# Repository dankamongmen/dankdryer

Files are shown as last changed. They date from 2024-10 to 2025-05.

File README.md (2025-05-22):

<p align="center">
ESP32, OpenSCAD, and KiCad sources for the Dankdryer, the world's best filament dryer.
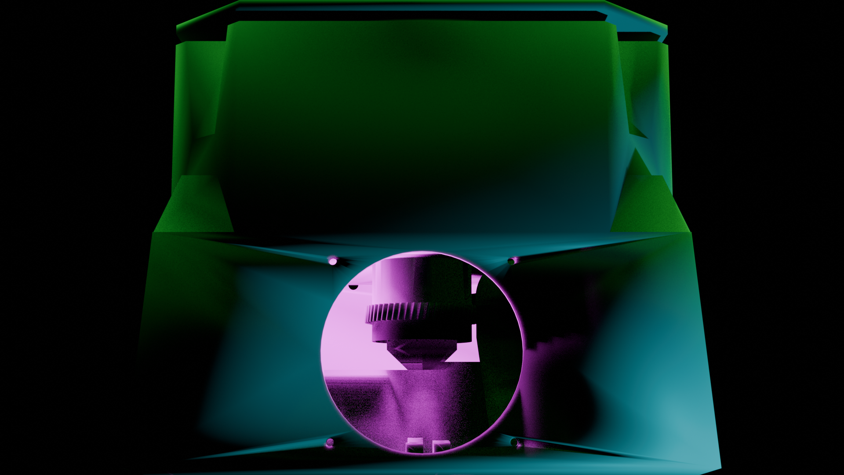
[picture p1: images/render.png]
Side view
 
 a nick black joint
</p>

# Features

* Temperatures up to at least 150℃  when printed with proper materials.
  * Such temperatures are appropriate (necessary) for certain engineering filaments.
  * A high-temperature spool is required at these temperatures.
* Accurate weight sensing throughout to determine how much water has been exorcised.
  * Post contextless deltas to reddit in the heat of dumbass arguments! DATA, bitch!
* Slow rotation like delicious savory meat.
* Equal heating of all the spool's filament.
* Control and reporting over MQTT via WiFi.
* OTA firmware upgrades.
* Isolated hot and cool chambers, with most active equipment in the cool chamber.
* Humidity sensing and temperature sensing in both chambers.
* Entirely open source.

More info at [dankwiki](https://nick-black.com/dankwiki/index.php/Dankdryer).

# Dependencies

The project is built with GNU Make.
Running `make` in the toplevel will attempt to build firmware and STLs.
Building the firmware requires the `esp-idf` library and a configured
ESP-IDF environment (i.e. the various `IDF_*` environment variables
must be set), along with CMake. `idf.py` ought be in your `$PATH`,
and work when invoked.

## Firmware
* [esp-idf](https://github.com/espressif/esp-idf) 5.3+
* [CMake](https://gitlab.kitware.com/cmake/cmake) 3.16+

## 3D models
* OpenSCAD 2024.10+

I use
[BOSL2](https://github.com/BelfrySCAD/BOSL2), which
is included as a submodule.

## PCB
* KiCad 8+

# Construction / BOM

The device as designed requires approximately 600g of high-temperature filament
(PA6-CF, PA6-GF, PAHT-CF, etc.) to print. The exact amount of filament will
depend on material and print settings. Six pieces must
be printed:

 * Hot chamber
 * Cool chamber
 * Top
 * Motor sheath
 * Sheath coupling
 * Spool platform

The hot and cool chamber dominate filament consumption, though the top is
non-negligible.

### Hot chamber

* [230C 110V ceramic heating element](https://www.amazon.com/dp/B0BXNPXXYW)
* [KSD301 175C NC thermal control](https://www.aliexpress.us/item/2251832675942217.html)
* [Hall sensor](https://www.digikey.com/en/products/detail/diodes-incorporated/AH3712Q-P-B/19920700)
* Custom PCB (fabrication cost is negligible; see components below)

We need a temperature sensor and hall effect sensor (and obviously the
heating circuit) in the hot box; nothing else ought be there.

### Cool chamber

* [Greartisan 5RPM 12V DC motor](https://www.amazon.com/dp/B072N867G3/)
* [NEMA plug + rocker switch](https://www.amazon.com/ASHATA-Rocker-Switch-Adapter-Printer/dp/B085VSS1F2)
* [160W 12V AC adapter](https://www.amazon.com/gp/product/B0D7GMVK2F)
* [8dBi antenna](https://www.aliexpress.us/item/3256807262687553.html)
* 5kg bar strain load cell
* 2-to-4 cable splitter
* Custom PCB (fabrication cost is negligible; see components below)

#### PCB components

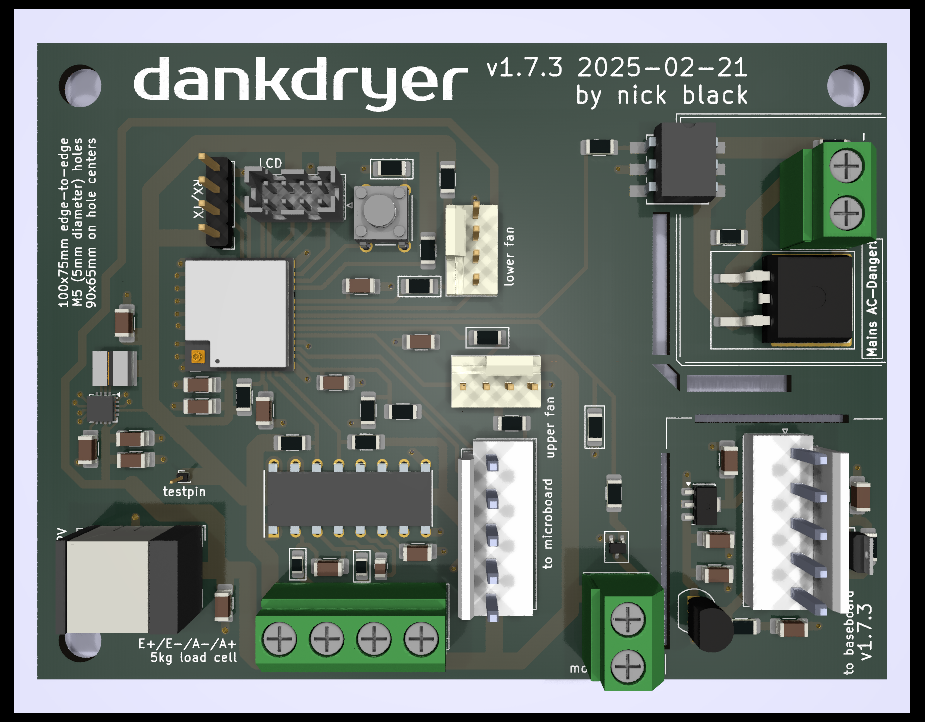
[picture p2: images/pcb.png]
Custom PCB


Generated via Kicad:

|Designator|Footprint|Quantity|Designation|
|---|---|---|---|
|U1|TPS62132|1|TPS62132|
|R4|R_1206_3216Metric_Pad1.30x1.75mm_HandSolder|1|360|
|R2|R_1206_3216Metric_Pad1.30x1.75mm_HandSolder|1|620|
|R6,R8|R_1206_3216Metric_Pad1.30x1.75mm_HandSolder|2|4.7k|
|C15,C16|C_1206_3216Metric_Pad1.33x1.80mm_HandSolder|2|1n|
|SW2|SW_B3F-1000_OMR|1|bootmode|
|R13,R20,R15|R_1206_3216Metric_Pad1.30x1.75mm_HandSolder|3|10k|
|R5,R1,R22|R_1206_3216Metric_Pad1.30x1.75mm_HandSolder|3|680|
|C7,C3,C9,C8,C20|C_1206_3216Metric_Pad1.33x1.80mm_HandSolder|5|0.1u|
|U2|TRANS_AH3712-P-B_DIO|1|AH3712Q-P-B|
|C6,C13|C_1206_3216Metric_Pad1.33x1.80mm_HandSolder|2|22u|
|C10,C17|C_1206_3216Metric_Pad1.33x1.80mm_HandSolder|2|1u|
|IC1|DIP792W51P254L1905H53Q16N|1|NAU7802KGI|
|J10|FanPinHeader_1x04_P2.54mm_Vertical|1|lower fan|
|C19,C2,C1,C14|C_1206_3216Metric_Pad1.33x1.80mm_HandSolder|4|10u|
|J2|JST_VH_B5P-VH-B_1x05_P3.96mm_Vertical|1|to microboard|
|J4|TerminalBlock_bornier-2_P5.08mm|1|heater|
|J8|TerminalBlock_bornier-2_P5.08mm|1|motor|
|J7|FanPinHeader_1x04_P2.54mm_Vertical|1|upper fan|
|R9,R19|R_1206_3216Metric_Pad1.30x1.75mm|2|15k|
|U6|XCVR_ESP32-C6-MINI-1U-H4|1|ESP32-C6-MINI-1U|
|J11|PinHeader_1x01_P1.00mm_Vertical|1|testpin|
|R16|R_1206_3216Metric_Pad1.30x1.75mm_HandSolder|1|412|
|J13|BarrelJack_Wuerth_6941xx301002|1|barreljack|
|R7|R_1206_3216Metric_Pad1.30x1.75mm_HandSolder|1|1.62k|
|C4,C18|C_1206_3216Metric_Pad1.33x1.80mm_HandSolder|2|.01u|
|J5|TerminalBlock_bornier-4_P5.08mm|1|5kg load cell|
|R10,R11|R_0805_2012Metric_Pad1.15x1.40mm_HandSolder|2|47|
|U5|TO-92_Inline|1|LM35-LP|
|R3|R_1206_3216Metric_Pad1.30x1.75mm_HandSolder|1|100|
|L1|IND_IFSC_1515AH_VIS|1|2.2u|
|R14|R_1206_3216Metric_Pad1.30x1.75mm_HandSolder|1|3.3k|
|OC1|MOC306XS_LTO|1|MOC3063S|
|C12|C_1206_3216Metric_Pad1.33x1.80mm_HandSolder|1|3.3n|
|C11|C_0805_2012Metric_Pad1.18x1.45mm_HandSolder|1|470p|
|R21|R_1206_3216Metric_Pad1.30x1.75mm_HandSolder|1|68|
|J9|PinHeader_1x04_P2.54mm_Vertical|1|UART|
|J6|JST_PHD_B8B-PHDSS_2x04_P2.00mm_Vertical|1|LCD|
|J3|JST_VH_B5P-VH-B_1x05_P3.96mm_Vertical|1|to baseboard|
|Q3|TO-263-2|1|T1210-800G|
|Q2|SOT-323_SC-70|1|SSM3K127TU|
|R12|R_1206_3216Metric_Pad1.30x1.75mm_HandSolder|1|330|
|U3|SOT-89-3|1|HT7550|

# MQTT

MQTT is used to report status and to accept commands.

## Controls

* `NAME/control/tare`: tare using the last weight read
* `NAME/control/dry`: takes as argument a string "DRYS/TEMP", where DRYS and TEMP are unsigned integers
    specifying the number of seconds to dry, and the temperature to dry at. Any ongoing drying operation
    will be replaced with the newly specified one. Specifying zero for DRYS will cancel any ongoing
    drying operation.
* `NAME/control/lpwm`: takes as argument a hexadecimal number between 0 and 255, left-padded with zeroes
    so as to be exactly two digits, i.e. "00".."ff". Sets the lower fan's PWM.
* `NAME/control/upwm`: takes as argument a hexadecimal number between 0 and 255, left-padded with zeroes
    so as to be exactly two digits, i.e. "00".."ff". Sets the upper fan's PWM.
* `NAME/control/factoryreset`: takes no arguments. Blanks the persistent storage, disables the motor
    and heater, and reboots.

# Renderings

View from the top of the lower chamber by itself, with the AC
adapter and motor assembly present.

<p align="center">
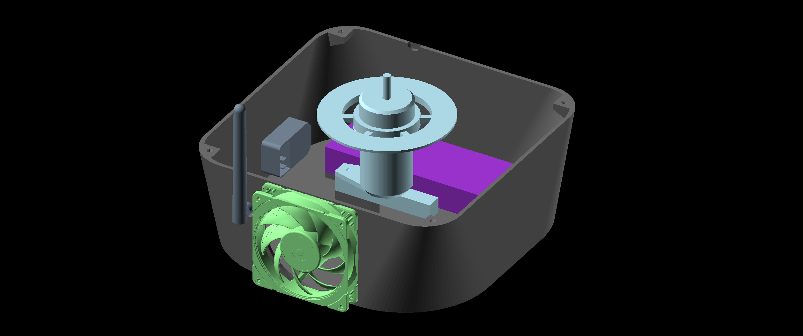
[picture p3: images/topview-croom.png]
Top view, lower chamber

</p>

Combined OpenSCAD render for mating testing.

<p align="center">
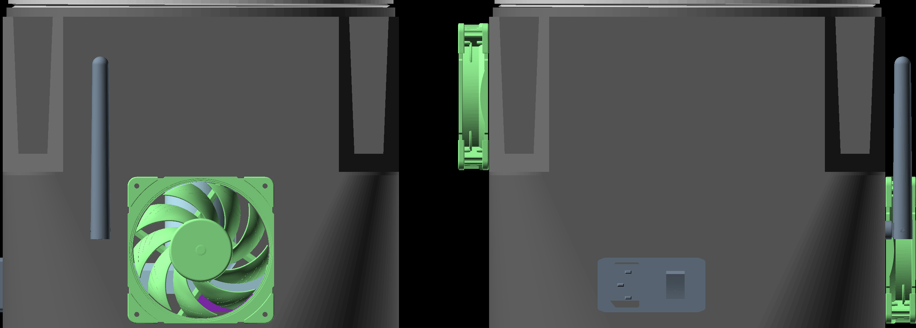
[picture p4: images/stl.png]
Combined render
 
</p>

# Questions

* How does air flow? Let's get some visible air and test it.
* What all could we accomplish by reading RFID?

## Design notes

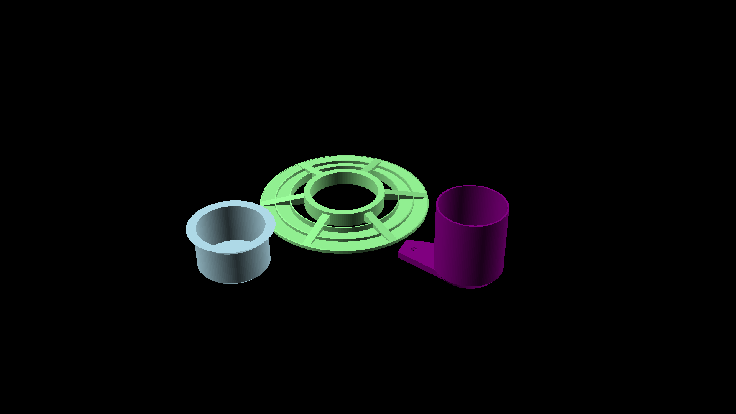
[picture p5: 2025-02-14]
webpage/coupling.png

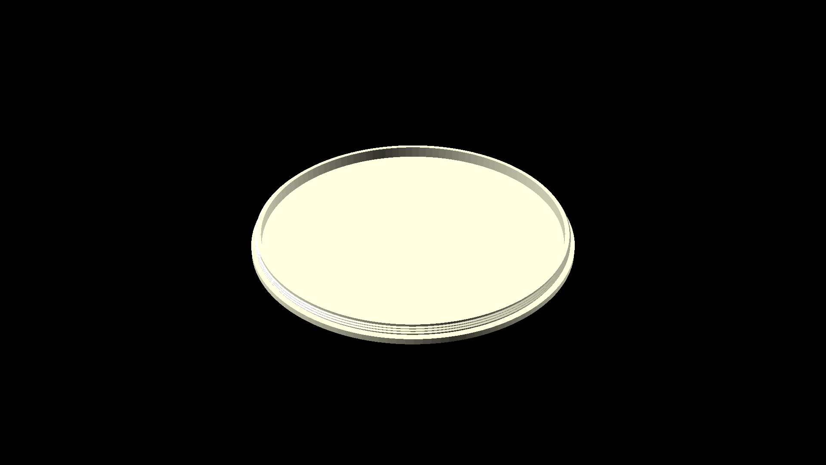
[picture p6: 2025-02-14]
webpage/top.png

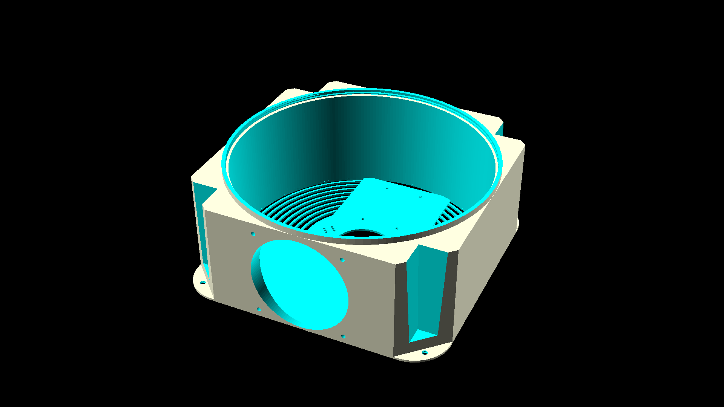
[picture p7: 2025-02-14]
webpage/hotbox.png

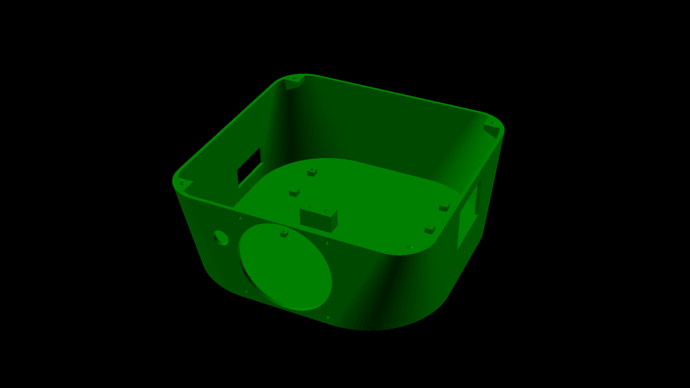
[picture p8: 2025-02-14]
webpage/croom.png

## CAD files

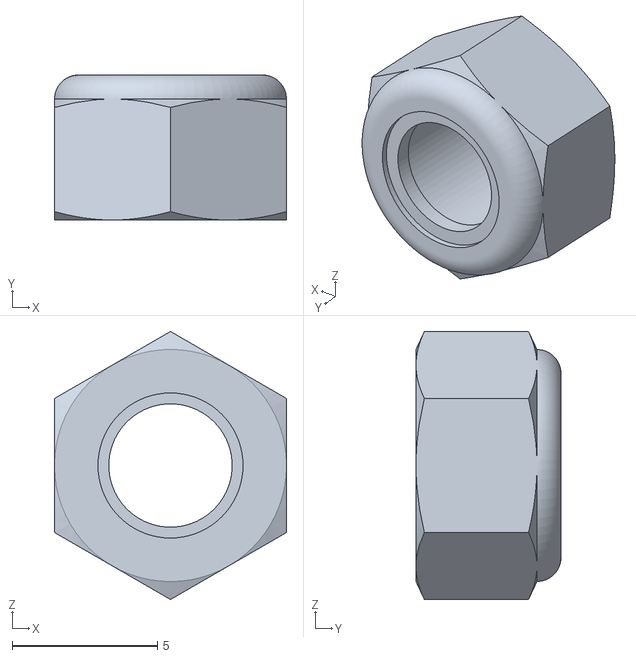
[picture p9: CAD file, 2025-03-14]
scad/m5nyloc.stl
8.00 x 5.00 x 9.24

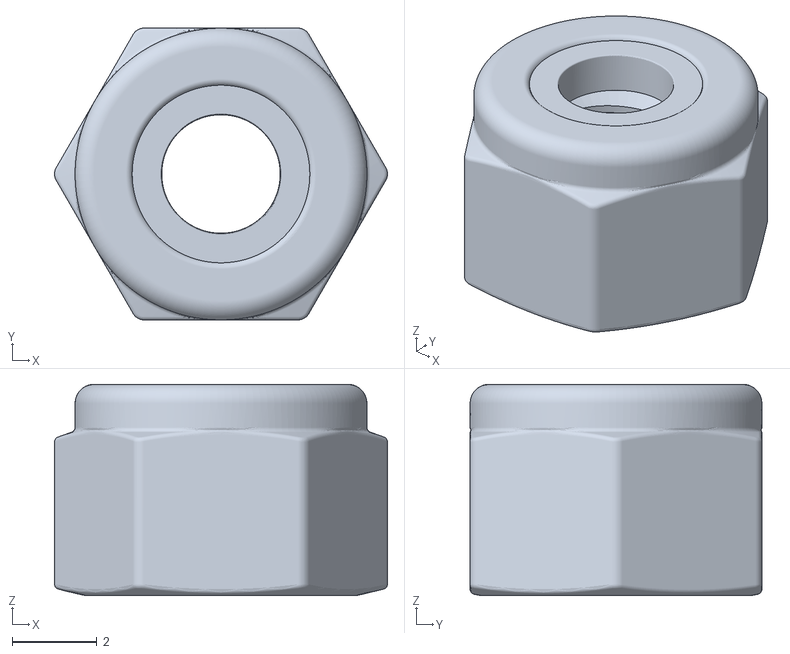
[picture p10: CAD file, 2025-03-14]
scad/m4nyloc.stl
7.87 x 6.90 x 5.00

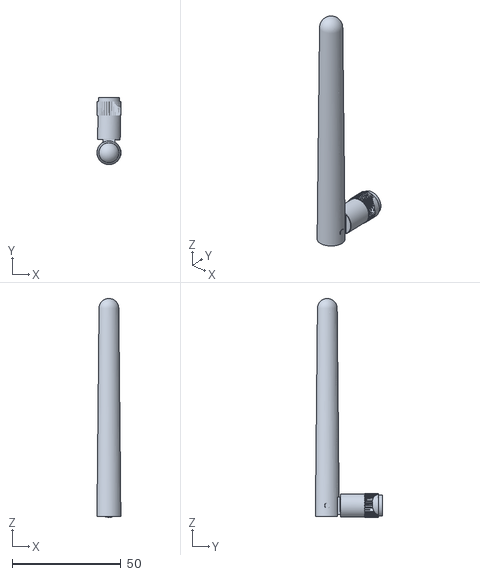
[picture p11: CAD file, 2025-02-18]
scad/antenna_WiFi_RP-SMA_conn.stl
11.1 x 30.9 x 100.5

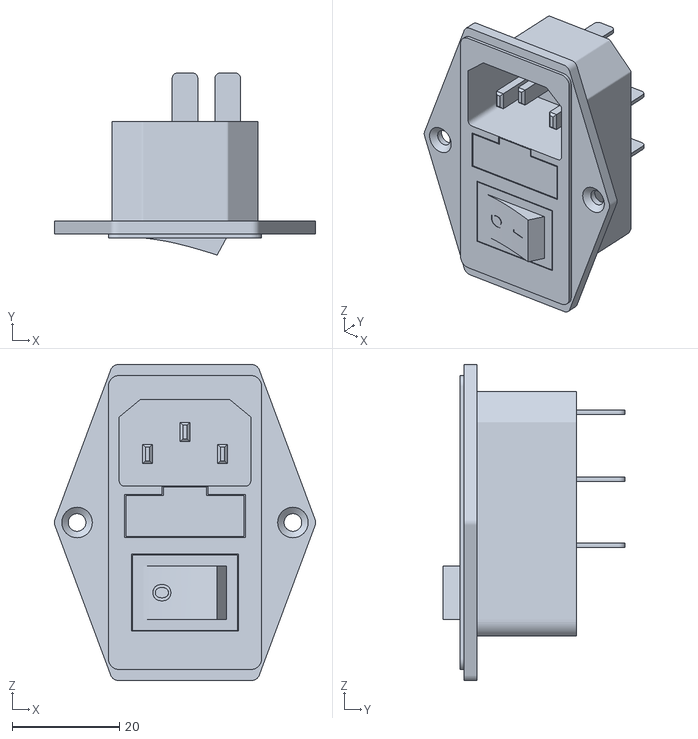
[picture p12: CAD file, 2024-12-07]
scad/iec.stl
48.8 x 34.0 x 59.0

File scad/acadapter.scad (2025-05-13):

include <core.scad>
include <BOSL2/std.scad>

// hole for four-prong rocker switch + receptacle.
// https://www.amazon.com/dp/B0CW2XJ339
// 45.7mm wide, 20mm high. if we can't print
// the bridge, we'll have to reorient it.
// model with fuse is 30mm
//rockerh = 20;
rockerh = 30;
rockerw = 46.3; // a bit of skoosh viz 45.7
module rockerhole(iech){
	translate([-botinalt - 2, 0, iech / 2 + 25]){
		rotate([90, 0, 0]){
			rotate([0, 180 - theta, 0]){
				difference(){
					cube([croomwall + 2, rockerw, rockerh], true);
					// two thin clips to hold the plug in
					// depth: 1mm height: 1.5mm
					translate([-1, 0, 0]){
						union(){
							translate([0, 0, rockerh / 2 - 0.75]){
								cube([1, rockerw, 1.5], true);
							}
							translate([0, 0, -rockerh / 2 + 0.75]){
								cube([1, rockerw, 1.5], true);
							}
						}
					}
				}
			}
		}
	}
}

//acadapterh = 30; // old model
acadapterh = 22;
acadapterw = 50;
acadapterl = 135;
acmounth = 6;

// the stand without the plug, since our AC
// adapters only have two places to screw
module acadapterstand(){
	translate([acadapterl / 2 - 0.5, -acadapterw / 2 + 7, acmounth / 2]){
		diff(){
			cuboid([8, 6, acmounth], 
					rounding=-1, edges=BOT)
				edge_profile(except=[TOP,BOT])
					mask2d_roundover(r=1);
		}
	}
}

// 60mm wide total
// screw holes are 6mm in from sides, so they start at
// 6mm (through 10mm) and 50mm (through 54mm)
// they have 2mm radius and 3mm height
module acadapterstands(){
	translate([0, acadapterw, 0]){
     	acadapterstand();
        mirror([0, 1, 0]){
			acadapterstand();
			mirror([1, 0, 0]){
				acadapterstand();
            }
        }
		mirror([1, 0, 0]){
			acadapterstand();
		}
    }
}

// hole in the AC adapter stand for screw
module acadapterhole(){
	translate([acadapterl / 2 - 0.5, -acadapterw / 2 + 7, 0]){
		holed = 3.6;
		ScrewThread(holed, acmounth);
	}
}

// screw holes for mounting ac adapter in two corners
module acadapterholes(){
	translate([0, acadapterw, 0]){
		acadapterhole();
		mirror([0, 1, 0]){
			mirror([1, 0, 0]){
				acadapterhole();
			}
		}
	}
}

module acadapter(){
	translate([0, 0, acadapterh / 2]){
		cube([acadapterl, acadapterw, acadapterh], true);
	}
}

/*difference(){
	acadapterstands();
	acadapterholes();
}*/
//acadapter();

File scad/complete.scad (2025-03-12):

include <core.scad>
use <hotbox.scad>
use <croom.scad>
use <coupling.scad>
use <top.scad>

multicolor("lightgreen"){
	translate([0, -109, -41]){
		rotate([theta, 0, 0]){
			rotate([0, 90, 90]){
				scale(17){
					import("noctua_nf-a12_fan.stl");
				}
			}
		}
	}
}

multicolor("black"){
	drop(){
		translate([0, 50, wallz]){
			acadapter();
		}
	}
	translate([-110, -30, -60]){
		rotate([0, 180 - theta, 0]){
			intersection(){
				rotate([270, 0, 0]){
					rotate([0, 0, 270]){
						import("iec.stl");
					}
				}
				cube([40, 120, 30], true);
			}
		}
	}
	translate([-55, -118, -35]){
		import("antenna_WiFi_RP-SMA_conn.stl");
	}
}

multicolor("dimgrey"){
    drop(){
        croom(20);
    }
}

multicolor("green"){
	drop(){
		pcb();
	}
}

multicolor("lightblue"){
    drop(){
        assembly();
    }
}

// top portion
if(!OPENTOP){
	rotate([0, 0, $t]){
		drop(){
			spool();
		}
	}

	multicolor("lightgreen"){
		translate([0, 109, 43]){
			rotate([0, 90, 90]){
				scale(17){
					import("noctua_nf-a12_fan.stl");
				}
			}
		}
	}

	multicolor("silver"){
			translate([0, 0, totalz + 2]){
					mirror([0, 0, 1]){
							top();
					}
			}
	}

	multicolor("dimgrey"){
			rotate([0, 0, 180]){
					hotbox();
			}
	}
}

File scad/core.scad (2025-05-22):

include <BOSL2/std.scad>
include <BOSL2/screws.scad>
use <threads.scad>

$fn = 128;

current_color = "ALL";

module multicolor(color, opacity=1) {
	//if (current_color != "ALL" && current_color != color) {
		color(color, opacity){
			children();
		}
	/*} else {
		// ignore
	}*/
}

module idtext(){
  text3d("v2.8.4", h=1.2, size=6);
}

// we need to hold a spool up to 205mm in diameter and 75mm wide
spoold = 205;
spoolh = 75;
// 80mm fan; use sin(theta)80 if we're sloped.
// 81 is a multiple of both 0.3 and 0.2.
hotz = 81;
spoolholed = 55;
tpitch = 1.8; // multiple of 0.3 and 0.2
// we'll want some room around the spool,
// but the larger our chamber, the more heat lost.
wallz = 1.8; // bottom thickness; don't want much
gapxy = 1; // gap between spool and walls; spool/walls might expand!
wallxy = 5;
// height of threaded, mated section at the top
// (and probably soon at the middle FIXME).
// ensure it's a multiple of both 0.2 and 0.3 to
// support both .4mm and .6mm nozzle layer heights.
ttopz = 0.2 * 0.3 * 100; // 6mm
// spool distance from floor and ceiling.
elevation = (hotz - spoolh) / 2;
chordxy = 33;
innerr = spoold / 2 + gapxy;
totalxy = spoold + wallxy * 2 + gapxy * 2;

ctopz = wallz;
croomz = wallz + ctopz + hotz;
totalz = hotz + wallz + ttopz + elevation;
locknuth = 5; // locknuts go atop mounting rods

// thickness of croom xy walls (bottom is wallz)
croomwall = 3;
// the outer radii on our top and bottom
botrad = totalxy * sqrt(2) / 2;
toprad = totalxy * sqrt(2) / 2;
// the inner radii on its top and bottom
botinrad = botrad - croomwall * sqrt(2);
topinrad = toprad - croomwall * sqrt(2);
// distances from center to mid-outer wall
topalt = toprad / sqrt(2);
botalt = botrad / sqrt(2);
topinalt = topinrad / sqrt(2);
botinalt = botinrad / sqrt(2);
botround = 90;
topround = 70;
adj = (botrad - toprad) / sqrt(2);
theta = (90 - atan(-croomz / adj));

flr = -croomz + wallz; // floor z offset
mh = wallz; // mount height
shieldw = 88;

module topbottom(height){
    linear_extrude(wallz){
        polygon(opoints);
    }
}

// cXcX3mm cube bottom plus (rh + th) d-wide riser
// rh is smooth length, th is threaded length
module mount(c, rh, th, d){
	ct = 3;
	translate([0, 0, ct / 2]){
		cube([c, c, ct], true);
		translate([0, 0, ct / 2]){
			RodStart(d, rh, th,
			         thread_diam=d - 0.5,
					 thread_pitch=0);
		}
	}
}

module foursquare(){
    children();
    mirror([1, 0, 0]){
        children();
		mirror([0, 1, 0]){
			children();
		}
    }
    mirror([0, 1, 0]){
        children();
    }
}

module rot(deg){
    rotate([theta + deg, 0, 0]){
        children();
    }
}

// spacing between the 4.3mm diameter holes is
// 71.5mm, so 8.5 / 2 == 4.25 from hole center
// to side. triangle with bases 2 * 8.5 == 17
module fanmountur(h){
    rotate([90, 0, 0]){
        // really want 4.3 but 4.5 is a multiple of
		// 0.3, and these will be horizontal
		// FIXME
		//ScrewThread(4.5, h, pitch=3);
		cylinder(h, 4.5 / 2, 4.5 / 2, true);
    }
}

module fanmountsider(h, d){
    translate([0, 0, d]){
        fanmountur(h);
    }
    mirror([0, 0, 1]){
        translate([0, 0, d]){
            fanmountur(h);
        }
    }
}

module fanmounts(h){
    r = 4.3;
    dist = 71.5;
    translate([dist / 2, 0, 0]){
        fanmountsider(h, dist / 2);
    }
    mirror([1, 0, 0]){
        translate([dist / 2, 0, 0]){
            fanmountsider(h, dist / 2);
        }
    }
}

//fanmounts(9);

module fanhole(h){
	fanmm = 80 - 5;
    rotate([90, 0, 0]){
        cylinder(h, fanmm / 2, fanmm / 2, true);
    }
    fanmounts(h);
}

//fanhole(9);

loadcellh = 12.7;
//loadcelll = 76;
loadcelll = 80;
// there is 5mm from each side to the center of
// hole closest to it, and 15mm between the centers
// of holes on a side. there are 40mm between the
// centers of the two inner holes. 80mm total.
loadcellmountholegap = 15;
loadcellmountholeside = 5;
loadcellmountholecgap = 40;
loadcellmountl = loadcellmountholeside +
                 loadcellmountholegap +
				 loadcellmountholecgap / 4;
loadcellmounth = 17;
loadcellsupph = 4;
loadcellmountw = loadcellh;
// we need the load-side holes of the load cell
// to be centered around the chamber center.
// the load-side center is at (loadcellmountholegap
// plus loadcellmountholeside) / 2.
loadcelloffx =
 (loadcellmountholegap + loadcellmountholeside) / 2
 - (loadcelll / 2);
module loadcell(){
    // https://amazon.com/gp/product/B07BGXXHSW
    cube([loadcelll, loadcellh, loadcellh], true);
}

// load cell mounting base with two threads
module loadcellmount(baseh){
    difference(){
		translate([0, 0, baseh / 2]){
			diff(){
				cuboid([loadcellmountl + 2,
						loadcellh + 2, baseh], 
						rounding=-5, edges=BOT)
					edge_profile(TOP)
						mask2d_roundover(r=2);
			}
        }	
        translate([-loadcellmountholegap / 2, 0, 0]){
			ScrewThread(5, baseh);
        }
        translate([loadcellmountholegap / 2, 0, 0]){
			ScrewThread(5, baseh);
        }
    }
}

//loadcellmount(loadcellmounth);

// height of inverse cone supporting bearing holder
couplingh = 10;
bearingh = 9; // height ("width") of bearing
bearingr = 30 / 2; // bearing outer radius
bearinginnerr = 10 / 2; // bearing inner radius
bearingwall = 2;
shaftr = bearinginnerr - 1;

module drop(){
    translate([0, 0, -croomz]){
        children();
    }
}

// motor is 37x75mm diameter gearbox and 6x14mm shaft
motorboxh = 70;
motorboxd = 37;
motorshafth = 40; // sans worm: 14
motortheta = -60;
motormounth = 61;
module motor(){
    cylinder(motorboxh, motorboxd / 2, motorboxd / 2, true);
    translate([0, 0, motorboxd]){
        cylinder(motorshafth, 6 / 2, 6 / 2, true);
    }
}

motorholderh = 3;
mlength = motorboxh + motorholderh;

module lowercoupling(){
	// the center must be in the dead center
	// of the structure.
	outerr = (motorboxd + 2) / 2;
	// we add 0.5mm for the polycarbonate (1 for
	// CF/GF), as it has no flex (0.25 to innerr)
	innerr = motorboxd / 2 + 0.25;
	// hole in middle to accommodate 10mm shaft
	holer = 10 / 2;
	boltheadh = 4;
	boltheadr = 3.5;
	th = loadcellsupph + boltheadh;
	couplingh = 40;
	// primary motor holder
	difference(){
		translate([0, 0, couplingh / 2 + loadcellsupph]){
			cylinder(couplingh, outerr, outerr, true);
		}
		translate([0, 0, loadcellsupph + couplingh / 2]){
			cylinder(couplingh, innerr, innerr, true);
		}
	}
	// fill in the bottom
	difference(){
		union(){
			cylinder(loadcellsupph,
					(motorboxd - loadcellsupph) / 2,
					outerr);
			translate([0, 0, loadcellsupph]){
				cylinder(boltheadh, outerr, outerr);
			}
		}
		cylinder(th, holer, holer);
		translate([0, 0, loadcellsupph + boltheadh / 2]){	
			// two M4 screws couple to the
			// load cell, but only the heads
			// remain
			// printing polycarbonate, which
			// tends to shrink). we then need
			// embed the 7x4 head in the floor
			translate([-loadcellmountholegap / 2, 0, loadcellsupph / 2]){
				rotate([180, 0, 0]){
					RodStart(boltheadr * 2,
							 boltheadh,
							 thread_len=loadcellsupph,
							 thread_diam=5);
				}
			}
			translate([loadcellmountholegap / 2, 0, loadcellsupph / 2]){
				rotate([180, 0, 0]){
					RodStart(boltheadr * 2,
							 boltheadh,
							 thread_len=loadcellsupph,
							 thread_diam=5);
				}
			}
		}
		// holes in the bottom for wires, polarity
		// legend, and also boltholes
		translate([0, 0, th / 2]){
			translate([0, innerr - 7, 0]){
				cylinder(th, 3, 3, true);
			}
			translate([0, -innerr + 7, 0]){
				cylinder(th, 3, 3, true);
			}
		}
		// designate positive side
		translate([4, -15, 0]){
			linear_extrude(th){
				text("+", size=7, font="Prosto One");
			}
		}
	}
}

/*bracel = loadcelll / 2 - loadcellmountl;
translate([-bracel + 3, 0, 0]){
	loadcellmount(loadcellsupph + 1);
}*/
//lowercoupling();
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

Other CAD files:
scad/coupling.scad
scad/croom.scad
scad/hotbox.scad
scad/lcd.scad
scad/lowercoupling.scad
scad/threads.scad
scad/top.scad

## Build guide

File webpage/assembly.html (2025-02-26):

# Assembly

## Not necessary for preassembled units!

Six objects are printed using four generated STL files. They ought be printed in the generated orientations.

- Top
- Upper (hot) chamber
- Lower (cool) chamber
- Internal components (load cell coupling, motor coupling, spool platform)

The OpenSCAD files can be found on Github (https://github.com/dankamongmen/dankdryer/tree/master/scad). The zipped STLs can be found here, and a 3MF is also available (https://nick-black.com/dankdryer.3mf). I print them with the Arachne perimeter generator and infill combination using cross hatch for the sparse infill. Using Polymaker Fiberon PA6-CF20 (nylon-6 + carbon fiber) with these settings, all components come in just over 600g.

Warp-free printing is essential. Warping of the internal components or the lower chamber can result in the spool not sitting level. Warping of the upper chamber can result in it failing to mate to the lower chamber.

1. Push the 175℃ thermostat through the bottom of the upper chamber.
2. Push the LM35 through-hole thermostat through the three small holes in the floor of the upper chamber.
3. Use four M4 screws to mount the ceramic heating element to the floor of the upper chamber.
4. Use four M5 screws to mount one of the 80mm fans to the outside of the upper chamber. The logo ought be facing out; this fan is an exhaust.
5. Insert the power plug/rocker switch unit into the rectangular hole on the side of the lower chamber. It ought not move once inserted. Secure it with hot glue.
6. Use two M5 screws to mount the AC adapter to the floor of the lower chamber, on the side opposite the intake fan.
7. Wire the plug/switch to the AC adapter.
8. Place the AC shield atop the AC wiring, and push it down. Secure it with hot glue.
9. Use four M5 screws to mount the PCB to the floor of the lower chamber, next to the intake fan.
10. Insert the antenna into the antenna hole to the left of the lower chamber's fan. Secure it with hot glue.
11. Connect the antenna to the U.FL connector on the PCB.
12. Use four M5 screws to mount the other 80mm fan to the outside of the lower chamber. The logo ought be facing in; this fan is an intake.
13. Connect the lower fan to the fan connector marked "lower" on the PCB.
14. Connect the upper fan to the fan connector marked "upper" on the PCB.
15. Use two M5 screws to mount the load cell to the central riser in the lower chamber.
16. Insert the motor into the motor coupling, ensuring the positive terminal mates to the hole marked '+'. The terminals ought go through the holes.
17. Wire the motor to the PCB.
18. Wire the heating element to the 175℃ thermostat.
19. Wire the heating element to the PCB.
20. Wire the 175℃ thermostat to the PCB.
21. Place the upper chamber atop the bottom chamber, matching the four holes.
22. Use four M5x35 bolts to securely mate the two chambers.
23. Push the spool platform down around the motor coupling.
24. Push the motor coupling down around the rotor and the top of the motor. The platform ought provide a level surface.
25. Place the top into the upper chamber.

### Contents of the kit

These are subject to change.

1. The Dankdryer PCB.
2. 120VAC → 12VDC adapter.
3. 2x 80mm 12VDC be quiet! Pure Wings 2 (https://www.bequiet.com/en/casefans/506) 4-pin fans.
4. 5kg load cell.
5. 12VDC brushed 5RPM motor.
6. NEMA plug + rocker switch.
7. RP-SMA antenna + U.FL adapter.
8. Wago 1x2→2x2 splitter.
9. 230℃ ceramic heating element.
10. 175℃ thermostat.
11. Roof microboard (currently perfboard + throughhole components).
12. Small bar magnet.
13. Bolts and appropriately preterminated wires.

copyright © nick black 2024–2025

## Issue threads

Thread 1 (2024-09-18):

open up AC hole

dankamongmen, 2024-09-18:
the side hole for our ac cabling is too small. i think it's currently 5mm. 7mm is probably better. we might also want to see about moving it to the fan side, or putting a TPU gasket in there -- right now it's on a hotpath for air, and we'll likely lose some out of it.

dankamongmen, 2024-09-18:
A naive enlargement shows an obstruction on the top. What could this be?
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

dankamongmen, 2024-09-18:
yeah it starts around -72.3 whatever size we make the hole

dankamongmen, 2024-09-18:
are we maybe improperly tilted?

dankamongmen, 2024-09-18:
lengthening the cylinder eliminates this. that makes sense if we're shorter than the wall thickness, but then wouldn't we have seen it at 5?

we don't have an explicit calculation for wall thickness on the croom. i guess it would be `(0.05 * totalxy) / 2`? let's see what that is...5.325. and we were 10, so yeah, i don't think that makes sense. oh, our cylinder could be misplaced, though, yeah that's surely it. let's fix it the right way, then.

dankamongmen, 2024-09-18:
you know what? i think we're improperly titled, as well...

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

dankamongmen, 2024-09-18:
holy shit, i've been misunderstanding the effects of `scale()` this entire time. we're calculating different wall thicknesses at the bottom and top because *the walls have different thickness at bottom and top*, with the wall being thinner at the top. think of it: scaling to 95% everywhere doesn't hold the wall thickness constant, dumbass. but we've been thinking it would for whatever reason.

alright, rather than using `scale()`, use `hull()` and two `polygon()`s. update everything that works off 0.95 multipliers. use the same radii to the outer walls that we have now:

```c
toprad = outerxy / 2;
botrad = totalxy * sqrt(2) / 2;
```

with a `$fn=4` instance of `cylinder()`, then a polygon at `0.95 * botrad`, then a polygon at `toprad - 0.05 * botrad`, with a `hull()` over it. actually, no---`botrad` is distinct from `botrad - croomz`, which is where we want the recess to start. ok, the right triangle drops an altitude from the `toprad`. that hits an outer corner via `sqrt(2) * (0.05 * botrad)`. oh wait we can do this more easily: `-flr / croomz * sqrt(2) * (0.05 * botrad)`

ok i'm just goin to redefine this more sensibly:
```
totalxy = spoold + wallxy * 2 + gapxy * 2; // hotbox altitude * 2. unchanged.
outerxy = (totalxy + 14) * sqrt(2); // hotbox radius. unchanged to reduce invalidations, though arbitrary
toprad = outerxy / 2; // unchanged
botrad =
```

dankamongmen, 2024-09-18:
ok, i've enlarged it to 7mm diameter, and placed it so that there is no obstruction. but it's longer than it ought be. reduce it when we fix #13.

Closed 2024-09-18.

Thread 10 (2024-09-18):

Design an air shield for the load cell

dankamongmen, 2024-09-18:
We cannot allow the fan to blow air over the load cell, as it would disturb our readings. Instead, there ought be an air shield surrounding (but *not* touching) the central shaft. The gear needs to be accessible by the motor, so we'll either need some gap in the air shield, or for it only to go up to the gear. I'm not sure which is better. If it does go all the way up, it ought mate to the central hole in the hotbox. In that case, we'd probably just want corner mounts for the shield where it intersects the gear. In no case ought fasteners be required (except to mount the shield to the croom's bottom).

dankamongmen, 2024-09-20:
Rather than being a distinct part, let's fold this into the lower mount and the croom. The bottom can be a part of the croom, so long as it fits inside the top part of the shield. This will eliminate a part and four screws, strengthen the shield, and make the lower coupling easier to print.

dankamongmen, 2024-09-20:
Though this might make it difficult to attach the load cell to the croom...

dankamongmen, 2024-09-20:
i think we can actually just put the entire thing on the croom, so long as we leave room on the lower coupling to stick an allen wrench down there and secure the load cell to its mount. i've gone ahead and made that change to the LC, which i think is an improvement in any case simply due to less material/weight.

dankamongmen, 2024-10-15:
it's there now, as part of croom.

Closed 2024-10-15.

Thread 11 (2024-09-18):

Design the central shaft

dankamongmen, 2024-09-18:
We need a central shaft on which the magic can happen. It ought fit within the air shield (see #10). It must be mounted to the load cell. It should be as light as possible. It must not receive support from anything but the load cell, or our weight sensing will get wrong results. I'm imagining an upside-down L mounted to the load cell's side and coming out to the center. It then expands into a walled recess into which a bearing is placed. From that bearing arises the central driveshaft. There will be a spacer, then the central gear (and see #10 regarding its effects on shield design). At the top, it expands into a platter onto which the spool will be placed.

Considerations:
* the platter is significantly wider than the shaft. How do we make this stable?
* Right now, the load cell is mounted to the floor of the croom. Any height by which we elevate it reduces the height of the shaft, adding stability. How tall can we take it? The motor would need be elevated a corresponding amount.
* How to keep the spool from moving?

dankamongmen, 2024-09-22:
i think we ought print the platter distinct from the shaft itself, so let's go ahead and whip that up. it ought be a wide circle (maybe half the spool diameter) and a small circle (just about the central hole size) with a `hull()` taken over them. there ought be a hollow column, almost the small circle's size. then another hollow cylinder ought plug in, which can go into the middle of the spool. this way we can have multiple columns, one for each spool size, which will keep them from shifting.

dankamongmen, 2024-10-05:
alright, this is working!

Closed 2024-10-05.

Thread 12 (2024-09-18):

thicken hotbox walls and make croom walls thinner

dankamongmen, 2024-09-18:
Croom walls too thick, hot walls too thin. Let's do 5 up top (we should keep the floor at 3, I think) and 3 on the bottom. Right now I think we have the inverse. Better to do this sooner rather than later, as it likely has effects on numerous things.

dankamongmen, 2024-09-18:
so first we need change `wallxy` from 2 to 5. `wallz`, the hotbox bottom, is by the way 2 not 3; let's change that to 3. this will increase `totalxy` by 6 and `totalz` by 1. a lot of things key off of `totalxy`, which we can't really reduce (it's the sum of `spoold + wallxy * 2 + gapxy * 2`), so we'll need deal with that. on the plus side, maybe this will make #4 easier.

dankamongmen, 2024-09-18:
mounting holes remain perfectly lined up; i think we're good up top...we haven't thinned out the bottom yet, though.

dankamongmen, 2024-09-18:
i don't think we can thin out the bottom until we've addressed the changing thickness of those walls (see #1, which i'm going to move into its own bug -- done, #13). i reduced `gapxy` from 2 to 1 to get 2mm back.

dankamongmen, 2024-09-18:
the croom xy walls are now a mere 2mm.

Closed 2024-09-18.

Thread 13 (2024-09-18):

croom walls get thinner as they rise

dankamongmen, 2024-09-18:
See #1 for initial exploration. The thickness of the croom walls change along the z axis when we reduce it with `scale()`. Instead, define the core via explicit polygons and `hull()` operations. Per #12, the croom walls ought only be 3mm thick. They're currently 5.825mm at their widest point, and 5.475 at their thinnest. This thinning ought significantly reduce material and print time; making them the same thickness throughout ought significantly reduce complexity.

dankamongmen, 2024-09-18:
Once we've done this, we'll need recalculate angles for the fan mount and the AC adapter hole. This is thus a prerequisite for both #1 and #12.

dankamongmen, 2024-09-18:
the xy walls now enjoy constant thicc.

Closed 2024-09-18.

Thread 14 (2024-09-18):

report all status over mqtt

dankamongmen, 2024-09-18:
over mqtt, we need to report:

 * both chamber temps
 * fan pwms
 * fan rpms
 * motor status
 * heater status
 * time left on drying run
 * target temp
 * uptime
 * version

dankamongmen, 2024-10-07:
we're reporting everything we measure. as we measure more, we'll add them.

Closed 2024-10-07.

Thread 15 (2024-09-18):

allow configuration over mqtt

dankamongmen, 2024-09-18:
we need to allow the device to be configured over mqtt. at minimum, this would involve:

* set the absolute drying time remaining
* set the target temperature for any drying

the target temperature ought have a default of 80. the absolute dry time remaining ought have a default of 0.

dankamongmen, 2024-10-07:
we're now supporting `mpwm`, `lpwm`, and `upwm`. these are all low-level controls which i don't really intend to expose to the user, who ought be using `dry`, but this will allow us to test.

dankamongmen, 2024-10-07:
confirmed `lrpm` and `urpm` work properly!

Closed 2024-10-07.

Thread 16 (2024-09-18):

get on wifi and talk to mqtt broker

dankamongmen, 2024-09-18:
we don't currently get on the wifi. do so. it ought be done in the main loop, not `setup()`, because we'll need to reconnect. once that's done, add mqtt connection (and reconnection). necessary for #15 and #14. give feedback via the LED.

dankamongmen, 2024-09-19:
https://docs.espressif.com/projects/esp-idf/en/stable/esp32s3/api-guides/wifi.html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

dankamongmen, 2024-09-19:
let's do it without some intermediary library. Espressif ships their own MQTT client now, so we oughtn't need worry about deps in that stack.

dankamongmen, 2024-09-25:
i'm pretty certain our continuing issues are due to using the arduino-style project and build. let me try building one of their examples using `arduino-cli` and see what happens...

dankamongmen, 2024-09-25:
nope, i was able to build the esp-idf STA example and it connected to my wifi just fine, and pulled down an IP. hrmm...

dankamongmen, 2024-09-25:
ahhh, looks like we needed `esp_netif_create_default_wifi_sta()`. with that call, we properly pull a DHCP lease. alright, excellent.

dankamongmen, 2024-09-25:
yep, with that we are connecting to MQTT and broadcasting mDNS!

```
E..:....@.H...X...X....5.&.k.............mqtt.orthanc.....
19:05:52.609735 IP 192.168.88.1.53 > 192.168.88.165.59396: 48591* 1/0/0 A 192.168.88.1 (46)
E..J..@.@.U	..X...X..5...67..............mqtt.orthanc...................X.
19:05:52.685910 IP 192.168.88.165.60678 > 192.168.88.1.1883: Flags [S], seq 2910239765, win 5760, options [mss 1436], length 0
E..,....@.H...X...X....[.v......`............f
19:05:52.685935 IP 192.168.88.1.1883 > 192.168.88.165.60678: Flags [S.], seq 3594378784, ack 2910239766, win 64240, options [mss 1460], length 0
E..,..@.@.....X...X..[...=. .v..`...X.......
19:05:52.772859 IP 192.168.88.165.60678 > 192.168.88.1.1883: Flags [.], ack 1, win 5760, length 0
E..(....@.H...X...X....[.v...=.!P...U......>.J
19:05:52.772860 IP 192.168.88.165.60678 > 192.168.88.1.1883: Flags [P.], seq 1:41, ack 1, win 5760, length 40
E..P....@.H...X...X....[.v...=.!P....O...&..MQTT...x..ESP32_e1BE34..mora3..mora3
19:05:52.772902 IP 192.168.88.1.1883 > 192.168.88.165.60678: Flags [.], ack 41, win 64200, length 0
E..(i.@.@.....X...X..[...=.!.v.>P...p...
19:05:52.773098 IP 192.168.88.1.1883 > 192.168.88.165.49560: Flags [F.], seq 2903896275, ack 652620666, win 64196, length 0
E..(.;@.@.K...X...X..[......&.3zP.......
19:05:52.773113 IP 192.168.88.1.1883 > 192.168.88.165.60678: Flags [P.], seq 1:5, ack 41, win 64200, length 4
E..,i.@.@.....X...X..[...=.!.v.>P...P... ...
19:05:52.795505 IP 192.168.88.165.49560 > 192.168.88.1.1883: Flags [R.], seq 1, ack 1, win 32790, length 0
E..(....@.H...X...X....[&.3z....P...<.....M..z
19:05:52.868692 IP 192.168.88.165.5353 > 224.0.0.251.5353: 0 [3q] [2n] ANY (QU)? Higher Dryer webserver._http._tcp.local. ANY (QU)? dankdryer0.0.1.local. ANY (QU)? dankdryer0.0.1.local. (120)
E....	........X............z.............Higher Dryer webserver._http._tcp.local......dankdryer0.0.1.......9.......!.....x.......P.9.9.......x....X.
19:05:52.875880 IP 192.168.88.165.60678 > 192.168.88.1.1883: Flags [.], ack 5, win 5756, length 0
E..(.
..@.H...X...X....[.v.>.=.%P..|T.....k#..
19:05:53.167950 IP 192.168.88.165.5353 > 224.0.0.251.5353: 0 [3q] [2n] ANY (QM)? Higher Dryer webserver._http._tcp.local. ANY (QM)? dankdryer0.0.1.local. ANY (QM)? dankdryer0.0.1.local. (120)
```

Closed 2024-09-25.

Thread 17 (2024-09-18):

support OTA

dankamongmen, 2024-09-18:
we'll need be able to load new versions of firmware onto the ESP32-S3. once we've got wifi working (se #16), add OTA capabilities.

dankamongmen, 2024-09-22:
this looks pretty complicated, with lots of partitioning and such. ideally we'll find a trustworthy library to handle this.

dankamongmen, 2024-09-22:
are we going to have the device pull OTA from the internet, or do we expect it to be sideloaded, or need we support both? pulling it over the internet will require PKI--at the very least, TLS and a cert store on the device. i think we have to support sideload given our "no cloud" guarantee. so let's handle that first. ideally we would have a random password per device, tied to the serial number, but that requires infrastructure as well...

dankamongmen, 2024-09-22:
yeah i think sideloading is the way to go, at least at first. we can optionally check to see if there's new firmware, and if we find it, let the user know. even that, though, would require PKI.

dankamongmen, 2024-09-22:
https://github.com/arduino-libraries/Arduino_ESP32_OTA explicitly claims esp32-s3 support

dankamongmen, 2024-09-22:
https://github.com/gb88/BLEOTA looks nice for using BLE ala nordic's DTU, but there's only one radio on esp32, so you can't use wifi and bluetooth at the same time. we'd probably want to switch to BLE update mode, and if we timeout, switch wifi back on. sounds pretty complex. let's keep looking...

dankamongmen, 2024-11-14:
we're now using `CONFIG_PARTITION_TABLE_TWO_OTA` via `menuconfig`, which ought generate the necessary partitions to support simple OTA.

https://docs.espressif.com/projects/esp-idf/en/stable/esp32/api-guides/partition-tables.html

dankamongmen, 2024-11-16:
we needed step up to flavor country aka `CONFIG_PARTITION_TABLE_TWO_OTA_LARGE=y`. i verify that we have two partitions of equal size, one (the boot default) called `ota_0`, and the other `ota_1`:

```
[schwarzgerat](0) $ for i in ota_0 ota_1 ; do /home/dank/src/esp-idf/components/partition_table/parttool.py --quiet --port /dev/ttyACM1 get_partition_info   --part_list --partition-name $i | tail -n 1 ; done
0x20000 0x1a9000
0x1d0000 0x1a9000
[schwarzgerat](0) $
```

size is 0x1a9000, and offsets are 0x20000 and 0x1d0000.

dankamongmen, 2024-11-16:
hrmmm according to the csv we ought have five partitions:

```
[schwarzgerat](0) $ cat /home/dank/src/esp-idf/components/partition_table/partitions_two_ota_large.csv
# Name,   Type, SubType, Offset,   Size, Flags
# Note: if you have increased the bootloader size, make sure to update the offsets to avoid overlap
nvs,      data, nvs,     ,        0x6000,
otadata,  data, ota,     ,        0x2000,
phy_init, data, phy,     ,        0x1000,
ota_0,    app,  ota_0,   ,        1700K,
ota_1,    app,  ota_1,   ,        1700K,
[schwarzgerat](0) $
```

dankamongmen, 2024-11-16:
hrrmmm, and indeed we do:

```
[schwarzgerat](0) $ for i in nvs otadata phy_init ota_0 ota_1 ; do /home/dank/src/esp-idf/components/partition_table/parttool.py --quiet --port /dev/ttyACM1 get_partition_info   --part_list --partition-name $i | tail -n1 ; done
0x9000 0x6000
0xf000 0x2000
0x11000 0x1000
0x20000 0x1a9000
0x1d0000 0x1a9000
[schwarzgerat](0) $
```

dankamongmen, 2024-11-16:
so it looks like we just need call `esp_ota_begin()` with the next OTA partition, call `esp_ota_write()` (possibly many times), call `esp_ota_end()` if that succeeds, then call `esp_ota_set_boot_partition()` and reboot.

this, however, only writes one partition. do we want to write both, so that one can fail and we still run the newer code?

dankamongmen, 2025-02-01:
it looks like it'll be way easier to support pulling down an OTA than (securely) accepting one.

insecurely accepting one might not be outlandish, especially if combined with basic signatures.

i'd like to ensure there's a way for customers to install their own custom firmware via OTA.

dankamongmen, 2025-04-07:
ok, this is now of critical importance. i'm going to run through the 10 existing PCBs and hit each one with a UART, but without OTA, i'll have to UART them again for the next code upload. might be better to wait until this is in there in some usable form...

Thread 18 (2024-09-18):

sample load cell and provide calibration

dankamongmen, 2024-09-18:
we need sample the load cell to get weight information. getting good absolute numbers requires calibration. i'm not sure about deltas. i think we might need do temperature compensation, also. this all ought be done through the HX711.

dankamongmen, 2024-10-07:
i've written the code to do this, but we're not yet getting reliable measurements. i'm pretty sure the load cell is properly deployed. the datasheet suggests powering the HX711 with 5V, which we're going to need for the LM35 anyway, so let's go ahead and get a 5V bus (can we use the 5V pin on the ESP32-S3? they're pretty low current devices, microamps both). i got a quality sparkfun HX711 and want to test with that.

dankamongmen, 2024-10-30:
We're reading this over I2C now. Need to validate it.

Closed 2024-10-30.

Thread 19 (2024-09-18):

send PWM signals to fans

dankamongmen, 2024-09-18:
we need to send a PWM signal to the fans. this signal must be independent, and controllable via MQTT. we ought use some default when we start a drying run. this default ought also be configurable, and persistent.

dankamongmen, 2024-09-18:
we're now sending the specified pwm signal. we probably only ought run them when drying. we need hook up MQTT.

dankamongmen, 2024-09-24:
we're now hooked up with pin 4 controlling the lower chamber fan and pin 5 controlling the upper chamber fan.

Closed 2024-09-24.

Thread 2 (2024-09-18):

fan doesn't mount properly to croom

dankamongmen, 2024-09-18:
Attempting to mount the 80mm fan to the croom indicates that the holes are spaced too closely vertically. We need another few millimeters. Also, we might want to take the space in a few mm, to ensure there's no gap around it.

dankamongmen, 2024-09-18:
i've implemented a correct differential `fanhole()` object, and used it in hotbox. now to use it in croom.

dankamongmen, 2024-09-18:
switched croom to `fanhole()`, which fixes several bugs. we now have a fully symmetrical 17mm triangle in each corner with the 4.3mm hole at 4.25mm in from the sides. it ought mate perfectly. the one thing we still want to fix is the angle of the fanhole; that will be addressed by #1.

Closed 2024-09-18.

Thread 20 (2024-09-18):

read tach signal from fans

dankamongmen, 2024-09-18:
we need to reach the tach from each fan, and use it to compute RPMs, which will be reported over mqtt.

dankamongmen, 2024-09-18:
i'm setting up the ISRs as of 64fb513

dankamongmen, 2024-09-18:
we might want to use the PCNT capability of the esp32-s3: https://docs.espressif.com/projects/esp-idf/en/stable/esp32s3/api-reference/peripherals/pcnt.html

dankamongmen, 2024-09-25:
i've verified with the oscilloscope that we see the expected signal (2 ticks per rotation, ~20 ticks per second at PWM=64, ~76 ticks per second with PWM disconnected, dead on) running a 10K from our 3.3V line to the tach then to a 3.3K to our pin to a 0.1nF capacitor. i don't think our code is working properly, though, as i'm seeing no interrupts.

dankamongmen, 2024-10-07:
this appears to work just fine now. let's report 'em via mqtt! (see #14)

Closed 2024-10-07.

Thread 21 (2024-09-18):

need programmed control of heater

dankamongmen, 2024-09-18:
we need a way to enable and disable the heating element programmatically. i'm not sure how i've overlooked this, heh. i think a power MOSFET is the way to go, as a relay will both make noise and die after far fewer state changes. a triac would be even better, as i believe that would allow us to control the voltage. it would be better to run the heater continuously at a lower voltage than turn it off and on a bunch, if that is possible. but at a bare minimum, we need the ability to turn off the heater once the hotbox reaches the target temperature.

dankamongmen, 2024-09-22:
when we figure out what we're going with, be sure to update the BOM.

dankamongmen, 2024-09-27:
rather than lofting it above the perfboard in the croom, let's fasten it upside down to the bottom of the hotbox. that'll be much easier to print, and we can solder it to the other hotbox pieces more easily.

Closed 2024-10-30.

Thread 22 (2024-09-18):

need temp sensor in hotbox capable of high temperatures

dankamongmen, 2024-09-18:
we already have a temp sensor for the MCU built into the ESP32-S3, but we also want to measure the hotbox temperature. a DH18B20 is probably not suitable, as it's only rated up to 125C, and only retains full accuracy through 85C. i've got some LM35DZs which ought work, though they want 4--30V and are analog. either way, get a thermistor up there, hook it up to the ESP32-S3, and measure the hotbox temperature.

dankamongmen, 2024-10-29:
The LM35 is operating in a nasty thermal environment, and on about ten centimeters of poorly-shielded AWG22. Let's give it some bigger boxing gloves. Put a 0.1µF bypass capacitor across its power and ground leads. Put a 75Ω resistor and a 0.22µF capacitor in series between the signal and the wire. These recommendations come directly from the datasheet.

dankamongmen, 2024-10-29:
as of 7e28b07a we're getting plausible values from the LM35 in STP tests.

Closed 2024-10-29.

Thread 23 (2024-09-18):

support a setup mode where wifi is configured

dankamongmen, 2024-09-18:
if we ever want to let other people use this thing, we'll need some kind of wifi setup. this would probably best be done by:

* assigning each device a serial number (ideally random)
* print the serial number on the device
* spin up an AP using the serial number in the ESSID
* run a webserver that presents scanned networks
* allow a network to be selected, and a password specified
* iff we connect (and get an IP?) switch to running mode (STA only) and write config to pstore
* support reconfiguration via MQTT
* factory reset puts us back in AP mode

this is all post-MVP. i have no plan to sell these currently, and this would be at least a day's work.

dankamongmen, 2024-12-02:
perhaps bluetooth-LE would be a better way to do this? i.e. if not configured, start up the bluetooth controller and response to BLE commands. do so on a factory reset, also.

but that requires something which can talk BLE, whereas during the normal mode we serve on WiFi...

perhaps both the AP mode and BLE?

dankamongmen, 2024-12-02:
i don't think BLE + AP is possible, given that they both use the 2.4MHz radio.

dankamongmen, 2024-12-10:
we *can* run bluetooth and wifi at the same time, it appears. this might have some bad effects, though (does it lock bluetooth channel for instance?). let's try it. always run bluetooth.

so when we do not have an essid/psk configured, we put up bluetooth le gatt, with three characteristics: one for essid, one for psk, one for setup status. essid is read/write. psk is write-only. setup status is read only, with update notification.

setup statuses:
* 0: waiting for essid/psk
* 1: setting up wifi
* 2: wifi configured

in setup state 0, you can write to both essid and psk. in states 1 and 2 writes will be rejected. factory reset (see #24) takes us to state 0, and resets essid/psk in NVS. writing to both essid+psk takes us to state 1, and initiates wifi association + dhcp request. acquisition of dhcp lease takes us to state 2 and writes the values to NVS. timeout takes us to state 0 and cancels the wifi stack.

intermittent wifi failures once in state 2 do not change our state; only a factory reset does.

on boot, try to read the values from NVS. if they're present, we start in state 2 with wifi running. if not, we start in state 0 with wifi not running.

dankamongmen, 2024-12-10:
i'm assuming for now that there is no app, just `bluetoothctl` and GATTs. either way, if we returned some secret upon successful setup, they could use that secret to factory reset via bluetooth. we can't provcide factory reset via bluetooth currently because there's no authentication.

dankamongmen, 2024-12-12:
this is done as part of the work on #65. we just need figure out how to configure MQTT.

Closed 2024-12-12.

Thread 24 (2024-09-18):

support factory reset

dankamongmen, 2024-09-18:
support a factory reset that wipes the pstore (and *maybe* switches to original firmware, but probably not). this ought be able to be effected via some physical interaction, since the device might not be reachable over the network. post-MVP.

dankamongmen, 2024-11-21:
a448031 adds a `factoryreset` MQTT command

dankamongmen, 2024-11-21:
factory reset now:
* disables the motor
* disables the heater
* blanks the NVS partition

this all seems good, except maybe we want to preserve the boot count across a factory reset?

dankamongmen, 2025-01-05:
so we're good here, right? we just need a hardware interface, which is #69.

Closed 2025-01-05.

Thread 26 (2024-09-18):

thread all mounting holes

dankamongmen, 2024-09-18:
we want actual screw holes for mounting. get proper ones from BOSL2.

dankamongmen, 2024-09-20:
alright, i think i got all of them. we'll need test the diameters to make sure everything still works out, but the positioning ought be exactly the same. i've added a note re BOSL2 to `README.md`.

Closed 2024-09-20.

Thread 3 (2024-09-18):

Move AC adapter mounting holes apart horizontally

dankamongmen, 2024-09-18:
The vertical spacing seems to be dead-on for the AC adapter, but I think we need a few more mm horizontally. Also, our M4 screws don't seem to bottom out, allowing the adapter to slip around a bit. I think maybe we ought extend them through the bottom, and use them to add feet to the croom. After all, it's probably going to get hot, and we don't want that sitting directly on the supporting surface. If we do that, we'll need two matching holes mirrored across the x-axis, and of course to design some feet (they ought just be frustra with an M4 hole).

dankamongmen, 2024-09-18:
we want to expand by about one hole radius

dankamongmen, 2024-09-18:
the holes have a radius of 2, which is exactly what i was eyeballing. so let's go from 165.1 away from center to 166.1.

dankamongmen, 2024-09-18:
wait, it's divided by 2. actually we have an offset of -3, so let's just change that to -2 for a total of 2.

Closed 2024-09-18.

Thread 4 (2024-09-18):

Move motor mount away from the wall

dankamongmen, 2024-09-18:
The motor tower is too close to the wall, making it difficult to insert and mount the motor. Move it away about 5mm. We'll likely need to change the placing of the central gear to account for this.

dankamongmen, 2024-09-18:
hrrrrm, we need the worm gear to be tangent to the main gear, i believe perfectly, and that's not going to work if we move it any further in (unless we shrink the gear considerably, which maybe we ought do).

dankamongmen, 2024-09-18:
I shrunk the worm gear down, and moved the motor stand to another angle. It now hits the gear correctly, but it cuts through a significant part of the air shield. We'll either need a significantly more complicated air shield, or we'll need change the 80x80mm fan to 2x40mms (which will be much louder, and require two fan hookups)....this affects #10

dankamongmen, 2024-09-18:
i'm not sure this actually leaves any more space between the motor and the walls, btw. we might only be able to fix that via enlarging the croom, or shrinking the gear further. i'd like to do a sample print and see...we only need print the quadrant holding the motor.

dankamongmen, 2024-09-19:
verified that we're good now.

Closed 2024-09-19.

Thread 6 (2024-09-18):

Strengthen motor mount front

dankamongmen, 2024-09-18:
The motor front mount is only 2mm thick currently. It'll break with the least pressure. Strengthen it up. Also, I'm not sure it's large enough -- I had some trouble going through the center. Break it out and verify the front mount.

dankamongmen, 2024-09-18:
Actually, it's offcenter entirely!

dankamongmen, 2024-09-18:
synced it into place in 8439fd7 along with work on #4

Closed 2024-09-18.

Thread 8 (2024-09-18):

Locking mechanism for top

dankamongmen, 2024-09-18:
The top sits uncomfortably in the recessed ceiling of the hotbox; it could easily slip out and even away. We need some kind of latching mechanism. This mechanism must be simple enough to allow the top to be inserted or removed in a tool-free fashion nigh-instantaneously. Ideally it would spin in and out, I think, using a screw-like technique. This would presumably require making the hotbox's top circular, and we would need ensure that twisting always led to unscrewing of the top from the hotbox, as opposed to the handhold (by which we would perform the twisting).

dankamongmen, 2024-09-19:
i'm thinking i'd like our octagon to morph into a circle at the top...and this actually looks possible, with a little bit of programmatically generated OpenSCAD

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

dankamongmen, 2024-09-20:
got the morph from octagon to circle working perfectly! though zounds it's slow.

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

dankamongmen, 2024-09-20:
so now all we need to do is change the top to a disc, and put in cantilevers at the top of the hotbox, and we're good!

dankamongmen, 2024-10-15:
it locks in there now via friction

dankamongmen, 2024-12-29:
no it doesn't, and that's lame anyway. put in a screw. it only needs 2 levels or so--we ought have more than enough room. we definitely do on the top. yeah, we ought be fine.

dankamongmen, 2024-12-29:
i've updated the models. need to test this, which will have to wait a few days while i wait on replacement parts for my bambu =\.

dankamongmen, 2025-01-04:
tested and works perfectly!

Closed 2025-01-04.

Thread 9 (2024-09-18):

Replace heater mounts with mounting holes

dankamongmen, 2024-09-18:
The mounts we use for the heater break easily, and require a nut. Make them mounting holes instead, using short screws. This might require thickening the hotbox floor a bit, but I think we might want to do that anyway.

dankamongmen, 2024-09-18:
oh, this is done

Closed 2024-09-18.

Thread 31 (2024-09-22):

round corners on the bottom

dankamongmen, 2024-09-22:
The croom is being printed with polycarbonate, which tends to warp badly at the corners. Rounding them will look better, and work against this tendency. Round the bottom corners without changing the geometry (i.e. it still ought basically be a frustrum).

dankamongmen, 2024-09-22:
i've rounded it out, and am testing a print now. we did seem to break the croom manifold along the way, according to OpenSCAD (BambuStudio opens it fine), which we probably ought remedy.

dankamongmen, 2024-09-22:
These look good. Still have the manifold breakage---I want to fix that before closing this.

dankamongmen, 2024-09-23:
the manifold breakage is coming from `dropmotormount()`, but yeah, let's get it fixed.

dankamongmen, 2024-09-23:
furthermore, it's emerging from the front mount (to no one's surprise)

dankamongmen, 2024-09-24:
manifold is reunited, hurrah

Closed 2024-09-24.

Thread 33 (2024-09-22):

make gerber files suitable for manufacturing

dankamongmen, 2024-09-22:
if we intend to make more than a handful of these things, we'll want a custom PCB for them rather than having to solder a bunch of shit to perfboard. this is not necessary unless the kickstarter works out, but if it does, it immediately becomes MVP.

dankamongmen, 2024-10-10:
i've started work on this in Kicad. it'll take some learning to complete.

dankamongmen, 2024-11-25:
i've ordered five boards from pcbgogo =]

Closed 2024-11-25.

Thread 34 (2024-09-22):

place croom at z=0

dankamongmen, 2024-09-22:
the croom is currently constructed at z=flr, i.e. underneath the hotbox at z=0. this makes working with any of its parts in isolation annoying. base it at z=0 like everything else, and only offset it in `hotbox.scad` when included for testing. this will have no externally visible effects, but it'll make our own lives saner.

dankamongmen, 2024-09-22:
it's now sitting at z = 0, and i fixed up a few small errors along the way!

Closed 2024-09-22.

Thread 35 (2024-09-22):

find suitable printing service

dankamongmen, 2024-09-22:
if we intend to make more than twenty or so of these things, we're going to want a printing service to do it, assuming we can find one with a decent price using suitable materials. should the kickstarter go through, this becomes MVP.

dankamongmen, 2024-10-07:
if we're going to sell this, we'll just be selling the PCB. no need to sell printed material.

Closed 2024-10-07.

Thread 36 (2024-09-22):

mount 150C thermocouple in floor of hotbox

dankamongmen, 2024-09-22:
We need to introduce a 150C normally closed thermocouple to our AC heater loop. Let's take the wire hole for the heater, and instead feed them through a hole next to the thermocouple, which will be placed below the right column of floor vents. There will need be a hole big enough for the thermocouple main plus its terminals. It'll sit with its top aligned with the hotbox floor, its ass hanging through the coolbox ceiling, suspended by its mounts, which will be screwed in.

dankamongmen, 2024-09-22:
i think we got it, just need to test.

Closed 2024-09-22.

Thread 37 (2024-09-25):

find cheaper motor

dankamongmen, 2024-09-25:
Our current motor is waaaaay overpowered, and costs $15. We ought be able to get a low-power brushless DC motor for a tenth of that. Select one, ensure it has enough torque, and adapt the motor mount and worm gear to it.

dankamongmen, 2024-10-07:
i ordered a sack of cheaper monitors, something like 8 for $18, an order of magnitude less than the Geartisan. note that they are brushed, as opposed to brushless.

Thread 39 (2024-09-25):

try to switch over to ESP32-S3 MCPWM, eliminating need for TB6612FNG

dankamongmen, 2024-09-25:
the TB6612FNG eats a lot of area on our perfboard, and contributes $3.33 to our BOM. the esp32-s3 has a MCPWM that might be able to replace it: https://docs.espressif.com/projects/esp-idf/en/stable/esp32s3/api-reference/peripherals/mcpwm.html

attempt to do so.

dankamongmen, 2024-09-27:
looking at the documentation, it appears that a motor controller is still necessary (see e.g. "capture").

Closed 2024-09-27.

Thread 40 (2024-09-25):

floating cantilevers in hotbox

dankamongmen, 2024-09-25:
The hotbox is loose with floating cantilevers, due I think to the top structure. Fill in the space underneath it. Right now it prints with strings and gaps due to the lack of support.

dankamongmen, 2024-09-25:
I got most of it in 20e5bd804c7dafdd779e35e829f118123cf2ae26. We still have some overhang, which I think we need just get rid of. Take the `difference()` of a core cylinder from `core2()`.

dankamongmen, 2024-09-25:
these are resolved in a8cf26e, at the cost of dumping `core2()` entirely from the hotbox. i'm cool with that--it was causing us other problems. i'd like a bit of styling to replace it, though. maybe a ziggurat kinda deal.

Closed 2024-09-25.

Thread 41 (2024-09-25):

need a hole in croom to feed hotbox fan cable through

dankamongmen, 2024-09-25:
The hotbox fan's cabling runs out of its front, which is sitting outside of the hotbox. We need a way to get this cable to the croom and plugged into the second fan plug. I think a small depression in the top of the croom would be the best way to do this. This should be on the AC adapter side, 40mm to the right of center. It needn't be as large as the plug, just the wires, so let's call that...a cylinder 1.5mm in radius.

Closed 2024-09-25.

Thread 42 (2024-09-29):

floating regions persist in croom

dankamongmen, 2024-09-29:
When we slice the croom in Bambu Studio, we get a floating cantilevers warning. I thought this due to the fan hole and not a real issue, but the hotbox (with the same fan hole) doesn't generate this warning. Track it down.

dankamongmen, 2024-10-07:
this has been eliminated.

dankamongmen, 2024-10-23:
nope, they're still there. i'm pretty certain they're coming from the corners.

dankamongmen, 2024-10-23:
yeah look at this
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

dankamongmen, 2024-10-23:
i think we need to rotate the pyramid ala the wall.

Closed 2024-10-23.

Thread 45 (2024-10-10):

dryer doesn't reconnect to mqtt server after disconnect

dankamongmen, 2024-10-10:
Actually, it looks like we're not responding to pings, either, but the only error I see is the MQTT disconnect due to ping failure...

```
pwm-l: 192 pwm-u: 192
raw: 1356 948
scale: 3.996887 diffu: 15011683
tach-l: 2709 tach-u: 1894
MQTT: {"uptimesec":88141,"dtemp":23.10000038,"lrpm":2709,"urpm":1894,"lpwm":192,"upwm":192,"load":0,"mpwm":0}
E (88154369) mqtt_client: No PING_RESP, disconnected
esp32 temp: 24.100000 weight: 0.000000
pwm-l: 192 pwm-u: 192
raw: 1344 946
scale: 3.996848 diffu: 15011828
tach-l: 2685 tach-u: 1890
MQTT: {"uptimesec":88156,"dtemp":24.10000038,"lrpm":2685,"urpm":1890,"lpwm":192,"upwm":192,"load":0,"mpwm":0}
couldn't publish 103B mqtt message
E (88176372) esp-tls: couldn't get hostname for :mqtt.orthanc: getaddrinfo() returns 202, addrinfo=0x0
E (88176372) transport_base: Failed to open a new connection: 32769
E (88176376) mqtt_client: Error transport connect
esp32 temp: 23.100000 weight: 0.000000
pwm-l: 192 pwm-u: 192
raw: 1339 947
scale: 3.996317 diffu: 15013824
tach-l: 2673 tach-u: 1890
MQTT: {"uptimesec":88171,"dtemp":23.10000038,"lrpm":2673,"urpm":1890,"lpwm":192,"upwm":192,"load":0,"mpwm":0}
couldn't publish 103B mqtt message
```

from this point on, we fail on all attempts to send messages, and don't respond to pings at `dankdryer.orthanc`. note that the first error is:

`E (88154369) mqtt_client: No PING_RESP, disconnected`

and then we see:

```
E (88176372) esp-tls: couldn't get hostname for :mqtt.orthanc: getaddrinfo() returns 202, addrinfo=0x0
E (88176372) transport_base: Failed to open a new connection: 32769
E (88176376) mqtt_client: Error transport connect
```

so it looks like the real problem is probably at layer 3. perhaps actually layer 2, as we're not able to ARP up a MAC address for the resolved ip:

```
[schwarzgerat](0) $ ip n l 192.168.88.165
192.168.88.165 dev ixgbe1 FAILED
[schwarzgerat](0) $
```

dankamongmen, 2024-10-10:
hrmmm, it did eventually reconnect and resume transmission of messages.

```
E (89761024) esp-tls: couldn't get hostname for :mqtt.orthanc: getaddrinfo() returns 202, addrinfo=0x0
E (89761024) transport_base: Failed to open a new connection: 32769
E (89761028) mqtt_client: Error transport connect
couldn't publish 103B mqtt message
esp32 temp: 23.100000 weight: 0.000000
pwm-l: 192 pwm-u: 192
raw: 1965 1437
scale: 2.726179 diffu: 22008828
tach-l: 2677 tach-u: 1957
MQTT: {"uptimesec":89764,"dtemp":23.10000038,"lrpm":2677,"urpm":1957,"lpwm":192,"upwm":192,"load":0,"mpwm":0}
connected to mqtt
failure subscribing to mqtt mpwm topic
failure subscribing to mqtt lpwm topic
failure subscribing to mqtt upwm topic
esp32 temp: 23.100000 weight: 0.000000
pwm-l: 192 pwm-u: 192
raw: 1707 1313
scale: 3.125521 diffu: 19196799
tach-l: 2666 tach-u: 2050
MQTT: {"uptimesec":89784,"dtemp":23.10000038,"lrpm":2666,"urpm":2050,"lpwm":192,"upwm":192,"load":0,"mpwm":0}
```

and it now responds to pings...

Closed 2024-11-21.

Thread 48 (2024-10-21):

replace our tach counters with PCNT unit

dankamongmen, 2024-10-21:
we probably ought use the ESP32's PCNT functionality rather than our handrolled tach counters. see https://docs.espressif.com/projects/esp-idf/en/v4.3/esp32/api-reference/peripherals/pcnt.html. it can use IRAM, so we don't lose anything there.

dankamongmen, 2024-11-21:
i don't think these really add much value. they have a glitch filter, but it's just "reject pulses shorter than this", and it puts a lock on dynamic frequency scaling. let's just filter noise properly with a low pass filter on the PCB.

however, i think we can remove our interrupt handler from IRAM.

Closed 2024-11-21.

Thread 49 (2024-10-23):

make component mounts discrete from croom

dankamongmen, 2024-10-23:
rather than building the mounts into the croom proper, we ought just leave screw holes there. that way, you can attach the discrete mounts to the IC outside the box easily, and have them secure, and then drop the entire structure into the croom, feeling around until the bolts hit the holes. it also reduces material for the croom print and doesn't fault out the croom if one of the mounts breaks off.

dankamongmen, 2024-10-23:
also regarding the croom:
 * restore symmetry to top corners (one's wonky currently)
 * cut the motor mount higher
 * bring the bottom out to reduce the overhang

dankamongmen, 2024-10-23:
all of these have been done

Closed 2024-10-23.

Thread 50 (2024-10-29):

need a way to enter calibration mode for NAU7802

dankamongmen, 2024-10-29:
We definitely want to support external calibration using a known mass for the NAU7802. How will we enter this mode, and let it know how much mass we calibrated with?

Currently we're running the internal offset calibration on startup.

dankamongmen, 2024-11-21:
given that digikey has neither the NAU7802 nor the HX711 in stock, it seems we need a different ADC/scale. =\

dankamongmen, 2024-11-21:
there's the ADS1231IDR, $4.12@10 from mouser.

the AD7191 looks good too, but is $14.31 from digikey. AD7191BRUZ is $10.71 from mouser.

AD7191: https://www.analog.com/en/resources/app-notes/an-2505.html

mouser has the sparkfun hx711 board for for $9.95: https://www.mouser.com/ProductDetail/SparkFun/SEN-13879
and a Soldered hx711 for $7.95: https://www.mouser.com/ProductDetail/Soldered/333005

mouser also has the sparkfun nau7802 for $14.95: https://www.mouser.com/ProductDetail/SparkFun/SEN-15242 (with the spring terminals for the load cell)
and adafruit for $5.95: https://www.mouser.com/ProductDetail/Adafruit/4538

the sparkfun nau7802 has an ADD hookup, while the others don't seem to, and our current power plans (#55) do break out an analog 5V line for this purpose...but we want that for the LM35 anyway.

together with the load cell, the ADC (from these selections) adds quite a bit to our BOM. do we really need it?

dankamongmen, 2024-11-21:
the sparkfun HX711 board doesn't seem that bad a deal at $9.95. it has an analog VDD. https://www.mouser.com/ProductDetail/SparkFun/SEN-13879?qs=wwacUt%252BV97ucrk9vYOp3tw%3D%3D

the seeed studio hx711 is only $5, but has no analog input, and uses some weird hookup: https://www.mouser.com/ProductDetail/Seeed-Studio/101020712?qs=wnTfsH77Xs6TZev5XrDa8w%3D%3D

i think we're going to go with the sparkfun hx711

dankamongmen, 2025-03-14:
we now automatically perform the internal calibration whenever a relevant parameter is changed, as recommended by the datasheet (present in 2.0.0).

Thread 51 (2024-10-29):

perform at least software calibration of ADC

dankamongmen, 2024-10-29:
https://docs.espressif.com/projects/esp-idf/en/v4.4/esp32s3/api-reference/peripherals/adc.html goes into detail. apparently our response is completely non-linear across a good chunk of the upper range until we do software calibration. thankfully, it appears this can be done non-interactively.

dankamongmen, 2024-10-29:
i implemented it using `esp_adc_cali`, but that is apparently the Old Way. we need to use `adc_cali`.

dankamongmen, 2024-10-29:
we are doing this using the new API as of f0ea52b

Closed 2024-10-29.

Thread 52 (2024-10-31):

attempt to sync time using ntp

dankamongmen, 2024-10-31:
It looks like there's SNTP functionality in esp-idf. We probably ought use it to try and set the RTC to something real.

dankamongmen, 2024-10-31:
```
                                                                                                                          dankdryer
a drying comes across the sky                                                                                               
                                                                                                                            
   lpwm: 32 upwm: 32                                                                                                        
   lrpm: 0 urpm: 0                                                                                                          
   motor: off heater: off                                                                                                   
   mass: 0.000000                                                                                                           
   lm35: 38.644688 esp32s3: 27.700001                                                                                       
   dryends: 0                                                                                                               
                                                                                                                            
     --------------------------------------------------------------------------------------------------------------------------
                                                                                                                            
   Thu Oct 31 14:52:04 2024                
```

w00t! this only works currently if there's a valid NTP server in the DHCP options.

dankamongmen, 2024-10-31:
https://docs.espressif.com/projects/esp-idf/en/stable/esp32s3/api-reference/network/esp_netif.html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 explains how to use both a static server and DHCP-provided ones

Closed 2025-01-05.

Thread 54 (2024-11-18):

motor runs sometimes even when gpio is low

dankamongmen, 2024-11-18:
Sometimes the motor comes on when we power up, when it ought be off. I think this is due to the lack of a pulldown resistor on the motor input; let's try adding one, and see if this stops.

dankamongmen, 2024-11-18:
no, we don't need a pulldown. we're only floating for a moment on boot; after that, we're always setting a valid level.

if this is a RFP30N06LE MOSFET, the datasheet shows G, D, S. we have pin + resistor, motor-, and ground. should be right.

hrmmm.

dankamongmen, 2024-11-21:
note that it is possible this was our culprit (since removed):

```
[schwarzgerat](0) $ git diff
diff --git esp32-s3/main/dankdryer.c esp32-s3/main/dankdryer.c
index e863c4a..fdb3303 100644
--- esp32-s3/main/dankdryer.c
+++ esp32-s3/main/dankdryer.c
@@ -69,7 +69,7 @@ static const ledc_channel_t LOWER_FANCHAN = LEDC_CHANNEL_0;
 static const ledc_channel_t UPPER_FANCHAN = LEDC_CHANNEL_1;
 static const ledc_mode_t LEDCMODE = LEDC_LOW_SPEED_MODE; // no high-speed on S3

-static bool MotorState;
+static bool MotorState = true;
 static bool HeaterState;
 static uint32_t LowerPWM = 128;
 static uint32_t UpperPWM = 128;
[schwarzgerat](0) $
```

if we can't reproduce, this was probably the problem.

dankamongmen, 2024-11-27:
this has nothing to do with code. the motor runs even if the MCU is turned off, as soon as we turn on the AC power.

dankamongmen, 2024-12-18:
ok, i think we do need a pulldown of 10k actually.

dankamongmen, 2024-12-18:
i've added that to the schematics and pcb. testing now...

Closed 2025-01-05.

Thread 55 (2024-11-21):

work out PCB power situation

dankamongmen, 2024-11-21:
Currently we take in 12V directly as well as 5V via USB. We then run 3.3V devices off of the MCU. We need 12V, 5V, and 3.3V.

I think instead we'd rather:
 * use the onboard USB if we want USB (e.g. for loading code)
 * by default, deliver power to the MCU via the 3.3V pin (as recommended in the datasheet)
 * leave an option to power the MCU via USB when that's hooked up
 * take in only 12V, from the AC adapter
 * transform the 12V down to a digital 3.3V (buck converter) and an analog 5V (linear regulator) onboard
 * power the 5V devices (LM35, HX711 VADD) from the 5V directly from the linear regulator
 * power the 3.3V devices from either the MCU or the downstepped 3.3V

Buck converters add more ripple to the power, so it would be better to use the linear regulator for the 5V devices, which are all analog. This wastes a bit of power, but they're all very low-power devices. The only things eating much power (more than a handful of mA) are all 3.3V, and they'll have the efficient buck converter. The 12V will feed the motor and fans directly.

I think we can continue to use the MCU for 3.3V sensors. We've got:
 * HX711 DVDD
 * fan tachometers
 * motor MOSFET
 * heater triac

and these are all tiny draws.

dankamongmen, 2024-11-21:
#33 is dependent upon this

dankamongmen, 2024-11-21:
currently we have an external USB-C plug, which we'll eliminate. this also means we can get rid of the USBLC6-2P6. if we ever trade in the DevKit for the raw MCU, though, we'll need add this functionality (or something equivalent) back.

dankamongmen, 2024-11-25:
We eliminated the external USB-C plug. it's now just a barreljack bringing 12V to the board, which is fed through a buck converter for 3.3V digital and through a linear regulator for 5V analog. should work.

Closed 2024-11-25.

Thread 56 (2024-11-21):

gears aren't meshing properly

dankamongmen, 2024-11-21:
I don't think the gears are meshing properly, leading to too little revolution of the platform, and (worse) misleveling of the platform. We ought be able to put a level on the platform and have it rotate all the way around without the level ever going wonky.

dankamongmen, 2024-11-25:
ok, first off, i'd like to get rid of `scad/gears.scad` (which supplies the `worm_gear()` we've been using) and instead call the proper BOSL2 API through `BOSL2/gears.scad`.

dankamongmen, 2024-11-26:
rewriting these in terms of BOSL2 gears is proving nontrivial

dankamongmen, 2024-11-28:
i think the best solution to this requires mounting the motor vertically and using simpler gears (or even a belt)

dankamongmen, 2024-11-29:
yeah, fuck gears. what we're going to do is vertically mount the motor atop the center of the load bar, and just tare it out. we'll need design a mount, but we can get rid of the mount that's in the croom (this will be a much lighter mount, for a nice net savings of material). i think we ought also bring the PCB into the center of its side of the bottom chamber, so it's directly in front of the fan (this will shorten most wires, also, and make it easier to install the PCB). we'll eliminate both the worm and the worm gear (more material savings), and just mount the platform directly onto the rotor. we'll likely need a shorter platform, ~~and the rotor must not rise much above the ceiling -- the platform can be no lower than the start of the rotor.~~ the platform can start anywhere on the height of the motor simply by making a `_|--|_` shape (though this might be difficult to print). awesome!

dankamongmen, 2024-11-29:
we also drop the bearing from our BOM. this is a big win!

dankamongmen, 2024-11-29:
yep, we now come in at 241g using PA6-CF and a mere 221g using ABS, w00t!

dankamongmen, 2024-12-02:
i've completed both sides of the redesign in #63 and #64. we now rotate regularly. huzzah!

Closed 2024-12-02.

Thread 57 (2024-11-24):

occasional reboots due to LoadProhibited exception

dankamongmen, 2024-11-24:
every few hours, i noticed the bright LED firing off, leading me to believe the unit was rebooting. indeed it appears we are:

```
scale: 11.952206 diffu: 5019994.000000 lrpm: 0 urpm: 0
ADC1: converted 0 to 0 -> 0.000000
lm35: 0.000000
Guru Meditation Error: Core  0 panic'ed (LoadProhibited). Exception was unhandled.

Core  0 register dump:
PC      : 0x400556d5  PS      : 0x00060f30  A0      : 0x8200e3c8  A1      : 0x3fca88f0
A2      : 0x00000000  A3      : 0xfffffffc  A4      : 0x000000ff  A5      : 0x0000ff00
A6      : 0x00ff0000  A7      : 0xff000000  A8      : 0x00000000  A9      : 0x3fca8890
A10     : 0x00000000  A11     : 0x00000001  A12     : 0x3fc9b568  A13     : 0x3fc9b568
A14     : 0x00000008  A15     : 0x00000000  SAR     : 0x0000001b  EXCCAUSE: 0x0000001c
EXCVADDR: 0x00000000  LBEG    : 0x400556d5  LEND    : 0x400556e5  LCOUNT  : 0xffffffff

Backtrace: 0x400556d2:0x3fca88f0 0x4200e3c5:0x3fca8900 0x4200e5a1:0x3fca8920 0x420bf4b3:0x3fca8970 0x4037e385:0x3fca89a0

ELF file SHA256: c46b78f48

Rebooting...
���ESP-ROM:esp32s3-20210327
Build:Mar 27 2021
rst:0xc (RTC_SW_CPU_RST),boot:0x8 (SPI_FAST_FLASH_BOOT)
Saved PC:0x40375bdc
SPIWP:0xee
mode:DIO, clock div:1
load:0x3fce2820,len:0x18c4
load:0x403c8700,len:0x4
load:0x403c8704,len:0xd20
load:0x403cb700,len:0x2f10
entry 0x403c8928
```

dankamongmen, 2024-11-24:
`EXCVADDR: 0x00000000 ` if i understand things correctly, this is a good ol' fashioned null pointer dereference

dankamongmen, 2024-11-24:
note that this followed a lengthy series of

```
W (4264983) wifi:m f null

W (4265193) wifi:m f null

W (4265403) wifi:m f null

W (4265603) wifi:m f null

W (4265813) wifi:m f null
```

dankamongmen, 2024-11-24:
looks like this is coming from `cJSON_Print()` at line 1284 of `dankdryer.c` (that's the third address on the stacktrace, 0x4200e3c5)

dankamongmen, 2024-11-24:
holy shit shitty `cJSON_AddItemToObject()` doesn't return an error value =\

dankamongmen, 2024-11-24:
hrmm i don't think we're freeing up the JSON object we create, and the creation probably eventually fails. yuck!

dankamongmen, 2024-11-24:
yeah i think we need `cJSON_Delete()` for the object created by `cJSON_CreateObject()`

dankamongmen, 2024-11-24:
i changed the code to publish to mqtt every second, and quickly enough we generated:

```
couldn't stringize JSON object
ESP_ERROR_CHECK failed: esp_err_t 0x101 (ESP_ERR_NO_MEM) at 0x4208ac16
--- 0x4208ac16: phy_track_pll_init at /home/dank/src/esp-idf/components/esp_phy/src/phy_common.c:110 (discriminator 1)

file: "/IDF/components/esp_phy/src/phy_common.c" line 110
func: phy_track_pll_init
expression: esp_timer_create(&phy_track_pll_timer_args, &phy_track_pll_timer)

abort() was called at PC 0x4037d8e3 on core 0
--- 0x4037d8e3: _esp_error_check_failed at /home/dank/src/esp-idf/components/esp_system/esp_err.c:49

Backtrace: 0x40375c9d:0x3fcaffe0 0x4037d8ed:0x3fcb0000 0x40385c41:0x3fcb0020 0x4037d8e3:0x3fcb0090 0x4208ac16:0x3fcb00c0 0x4208ab09:0x3fcb0100 0x420bef4d:0x3fcb0120 0x4003ad27:0x3fcb0140 0x40387de9:0x3fcb0160 0x4038840a:0x3fcb0190 0x4003d021:0x3fcb01b0 0x403869b9:0x3fcb01d0 0x4037e385:0x3fcb0200
--- 0x40375c9d: panic_abort at /home/dank/src/esp-idf/components/esp_system/panic.c:454
0x4037d8ed: esp_system_abort at /home/dank/src/esp-idf/components/esp_system/port/esp_system_chip.c:92
0x40385c41: abort at /home/dank/src/esp-idf/components/newlib/abort.c:38
0x4037d8e3: _esp_error_check_failed at /home/dank/src/esp-idf/components/esp_system/esp_err.c:49
0x4208ac16: phy_track_pll_init at /home/dank/src/esp-idf/components/esp_phy/src/phy_common.c:110 (discriminator 1)
0x4208ab09: esp_phy_enable at /home/dank/src/esp-idf/components/esp_phy/src/phy_init.c:281
0x420bef4d: esp_phy_enable_wrapper at /home/dank/src/esp-idf/components/esp_wifi/esp32s3/esp_adapter.c:616
0x4003ad27: wifi_rf_phy_enable in ROM
0x40387de9: pm_dream at ??:?
0x4038840a: pm_tbtt_process at ??:?
0x4003d021: pm_on_tbtt in ROM
0x403869b9: ppTask at ??:?
0x4037e385: vPortTaskWrapper at /home/dank/src/esp-idf/components/freertos/FreeRTOS-Kernel/portable/xtensa/port.c:139

```

so it looks like we're right

dankamongmen, 2024-11-24:
i added the necessary `cJSON_Delete()`, and i expect this to be resolved

Closed 2024-11-24.

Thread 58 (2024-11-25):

current worm doesn't fit snugly on the rotor

dankamongmen, 2024-11-25:
somewhere along the line we fucked up our worm model (see also #56). get it back to fitting snugly on the rotor, with the d-shape. it's too loose right now; we only have the purple ABS, never intended for use, in service.

dankamongmen, 2024-11-25:
got this fixed in a17a6c6; freshly printed worm settles right on.

Closed 2024-11-25.

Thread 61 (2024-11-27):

replace moc3061m with some smd optoisolator

dankamongmen, 2024-11-27:
we're currently using a MOC3061M through-hole optoisolator (https://www.digikey.com/short/tfwrw5cw). find a native smd one and update our schematics/pcb. i guess we'd need manufacture new pcbs as well; make this part of v0.9.1.

dankamongmen, 2024-11-27:
maybe the moc3063s-ta1 would work? https://www.digikey.com/short/v079pwft pretty much an SMD equivalent

dankamongmen, 2024-11-27:
i've moved us over to the MOC3063S-TA1.

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

Closed 2024-11-27.

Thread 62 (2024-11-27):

assemble PCBs

dankamongmen, 2024-11-27:
we've got 5 v0.9 boards en route, and i'll probably order some v0.9.1 boards. get them populated!

- [x] get final BOM (deps on #61)
- [x] order tapes of necessary SMD components
- [x] use paul's pick-and-place to populate a v0.9 board
- [x] solder up v0.9 through-hole components
- [x] validate v0.9 board
- [x] order v0.9.1 boards following validation
- [ ] use paul's pick-and-place to populate a v1.1.0 board ((almost) all SMD)

dankamongmen, 2024-11-27:
ordered this morning from digikey:

| Part | Count |                                                                                                            
| ---- | ----- |                                                                                                            
| TPS62162DSGR IC REG BUCK 3.3V 1A 8WSON | 10 |                                                                             
| HT7550-1 SOT-89 MONITORS & RESET CIRCUITS | 10 |                                                                          
| MLZ2012M2R2HT000 FIXED IND 2.2UH 600MA 160MOHM SM | 50 |                                                                  
| CL21B106KOQNNNE CAP CER 10UF 16V X7R 0805 | 100 |                                                                         
| RK73H2ATTD3301F RES 3.3K OHM 1% 1/4W 0805 | 100 |                                                                         
| RK73H2ATTD6800F RES 680 OHM 1% 1/4W 0805 | 100  |                                                                         
| RK73H2ATTD2200F RES 220 OHM 1% 1/4W 0805 | 100  |                                                                         
| RNCF0805DTE330R RES SMD 330 OHM 0.5% 1/4W 0805 | 100  |                                                                   
| RK73H2ATTD3600F RES 360 OHM 1% 1/4W 0805 | 100  |                                                                         
| RK73H2ATTD1000F RES 100 OHM 1% 1/4W 0805 | 100  |                                                                         
| CL21C101JBANNNC CAP CER 100PF 50V C0G/NP0 0805 | 100  |                                                                   
| CL21B102JCANNNC CAP CER 1000PF 100V X7R 0805 | 100  |                                                                     
| BT136S-800E,118 TRIAC SENS GATE 800V 4A DPAK | 10 |                                                                       
| SSM3K127TU,LF MOSFET N-CH 30V 2A UFM | 10 |                                                                               
| 694108301002 CONN PWR JACK 2.5X5.5MM SOLDER | 10  |                                                                       
| MOC3063S-TA1 OPTOISOLATOR 5KV TRIAC 6SMD | 10 |

dankamongmen, 2025-02-28:
we got assembled PCBs from jlcpcb today!

Closed 2025-02-28.

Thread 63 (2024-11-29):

design new vertical mount for motor

dankamongmen, 2024-11-29:
see #56 for background. convert the lower coupling from holding a bearing to holding the motor vertically. it ought leave the bottom mostly open (for wiring), and probably sheath the motor at least halfway up its height. also, let's just directly mount this atop the load cell, rather than using the intermediary plane.

dankamongmen, 2024-11-29:
i think we can take the existing motor mount, turn it on its side, and give it a simple mount to the load cell. i don't think we need raise it at all; the load cell can go between the terminals and still leave enough room to hook them up. we can thin out the side mount, but keep it going all the way to the top, and continue to use the collar. we'll even be able to use all six screws now, so add the "bottom" (far side of the load cell) three back.

dankamongmen, 2024-11-29:
i've just about got it. need to put in the lower plane, and eliminate this weird flat part of the semicylinder.

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

dankamongmen, 2024-11-29:
got it, just need to hew away at the enclosed cylinder...

dankamongmen, 2024-11-29:
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

this is what we want, but it would be very difficult to print.

dankamongmen, 2024-11-29:
the only way i see this working, print-wise, is if we put in a triangular solid atop the brace, and print from the motor collar up. just extend the holes through whatever we make.

dankamongmen, 2024-11-29:
yeah we ought be able to just extend this as a triangle

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

dankamongmen, 2024-11-29:
hmmm, we can only deal with the load cell side that way, not the internal plane (our supports would otherwise collide with the motor). hrmmmm.

dankamongmen, 2024-11-29:
maybe cheat and use supports to validate the idea? but i'd like to stay away from supports in the end.

dankamongmen, 2024-11-30:
ok, see #64. we're not doing any of that. all we need on the lower side is a coupling that can snugly hold the bottom of the motor, while exposing its terminals. basically a diaper.

dankamongmen, 2024-12-02:
ok, i think we've got it (upper right)

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

dankamongmen, 2024-12-02:
works great!

Closed 2024-12-02.

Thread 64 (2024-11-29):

reconfigure platform to work with vertical motor

dankamongmen, 2024-11-29:
see #56 for background. we need adjust the platform so that it mounts to the rotor. depending on how high this goes, we might then need to drop the actual platform closer to the floor of the hot chamber.

dankamongmen, 2024-11-30:
current stage 1 design:

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

current stage 2 design:

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

we probably ought use a triangular beveling on stage 1, so we can do a triangular support for the stage 2 rim. stage 3 will be like the top of the old platform, with a mount that fits stage 2.

dankamongmen, 2024-11-30:
> we probably ought use a triangular beveling on stage 1, so we can do a triangular support for the stage 2 rim.

no need for this, since we're back to printing stage 2 from true top to bottom (i.e. inverted).

dankamongmen, 2024-11-30:
i've proven out rotation for stages 1 and 2. printing stage 3 now!

dankamongmen, 2024-12-02:
rotation proved for all three assembled stages. i think we're done here!

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

Closed 2024-12-02.

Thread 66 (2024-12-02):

bevel the rotor sheath

dankamongmen, 2024-12-02:
the inside rim of the cupola is triangle-beveled (a necessity to avoid supports), but there's no beveling on the sheath, and thus it sits poorly. put a 45deg angle on the sheath rim.

dankamongmen, 2024-12-06:
i did some basic bevelling, but the cupola can still shift--pretty easily, really. i think we need a secure binding here, and i'm thinking it's best done either with a solid friction fit or via a screw-top. i suspect that simply reducing the diameter of the cupola by 1-2mm would be a significant help.

dankamongmen, 2024-12-06:
keep the cupola's outer diameter untouched; it's perfectly sized for the platform, which i don't want to have to change.

dankamongmen, 2024-12-06:
eh, the cupola walls would then be very thick. go ahead and cut down both the cupola and the platform from `cupolaw + cupolat` to the intended `cupolaw` (which already includes `cupolat`).

dankamongmen, 2024-12-06:
i've tightened it up, and i can now pretty much drop a spool onto the platform from several inches up, put a level on it, and verify that it is level. i think we're good!

Closed 2024-12-06.

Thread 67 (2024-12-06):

replace sparkfun board with nau7802

dankamongmen, 2024-12-06:
rather than using a sparkfun hx711 sample board, we ought use a discrete NAU7802 or HX711 directly. i think i prefer the NAU7802, with its I2C interface. this isn't necessary for MVP, but we ought do it sooner rather than later. it'll also simplify PCB assembly.

dankamongmen, 2024-12-14:
updating the schematic now. itnerestingly, it says AVDD should not exceed DVDD. since our AVDD is 5V and our DVDD is 3.3V, i guess we're going with 3.3V for both -- i'm not putting another voltage regulator on there, certainly not from 12V to 3.3V. oh well!

dankamongmen, 2024-12-29:
i've substituted a NAU7802 in our schematics and PCB, and changed the code to use it.

Closed 2024-12-29.

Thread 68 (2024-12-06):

measure rotation of spool

dankamongmen, 2024-12-06:
if we could measure the rotation of the spool, that would be interesting to display, and we would want to know if it dropped to zero or simply below the expected value of ~5RPM.

this seems best done with a hall sensor, maybe? look into it. we don't need this for MVP.

dankamongmen, 2024-12-06:
huh, hall effect sensors are not very cheap.

this unit looks appropriate: https://www.mouser.com/ProductDetail/TDK-Micronas/HAL1501SU-A?qs=TiOZkKH1s2S8BvAk0HQMCQ%3D%3D except it's SMD and we probably need through-hole up in the hot box.

this throughhole is $0.53@10, supported up to 150C, and runs on 3V: https://www.mouser.com/ProductDetail/Diodes-Incorporated/AH3362Q-P-A?qs=lqAf%2FiVYw9hFmF68MMwGkw%3D%3D

digikey says it's no longer made, though.

the TLV49681TAXBXA1 is available at both mouser and digikey...digitkey says it's good to 150, but datasheet and mouser claim only 125.

AH3712Q: https://www.diodes.com/assets/Datasheets/AH3712Q.pdf up to 150C, takes 3--26V, 1.6mA supply, has both a throughhole and an SMD variant...i like it. $5.56 for 10 at digikey, $4.25 for 10 at mouser. let's get a few!

dankamongmen, 2024-12-06:
mouser has them on backorder, though. =\ pull from digikey i guess

dankamongmen, 2024-12-06:
so since this will be living in the hot chamber, we'll want to power it off the 5V analog line going to the LM35. that means we'll want to expand the 4-terminal to a 5-terminal (for the hall sensor data line) and bifurcate the +/- lines at the microboard. let's update the schematic and PCB.

dankamongmen, 2024-12-06:
schematic and PCB updated. we now have a 1x5 on the PCB and a 1x4 on the microboard.

dankamongmen, 2024-12-29:
i've updated our schematics for both a throughhole and an SMT microboard. i don't know whether we'll manufacture a PCB for this; perfboard ought work fine. but i validated both. we need to write the code to support the hall sensor, but everything electronic ought be working.

dankamongmen, 2024-12-29:
I've updated the firmware to install an interrupt on the Hall sensor pin, count pulses, and report them in mqtt/http.

All we need now is to add a magnet to the spool platform for the Hall sensor to sense.

Closed 2024-12-29.

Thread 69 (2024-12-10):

need a hardware interface to factory reset

dankamongmen, 2024-12-10:
we've got factory reset logic due to #24. we have no way to invoke this code, though, save over mqtt. we need a hardware interface, probably a button on the inside of the device. to improve this, we'd have something recessed (but available with a long, thin tool) from the outside. an internal button is fine for now.

dankamongmen, 2025-03-16:
we can just reuse the boot selection button for this purpose, since it will only be functional after we've booted.

install an interrupt handler. in this handler, check for the pin going low. if it goes low, set a global variable to the current time. if it goes high, set the global variable to a sentinel. we don't need to worry about debouncing, since the last state will always be low for a factory reset. then, in the main loop, check to see if the global variable is not the sentinel. if it is not, check to see if it is more than 5s ago. if so, engage the reset.

Closed 2025-04-07.

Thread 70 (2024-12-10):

some kind of external visible feedback

dankamongmen, 2024-12-10:
we need at least, like, an LED on the outside so we can distinguish between:

* unpowered
* setup
* connected, not drying
* connected, drying
* disconnected, not drying
* disconnected, drying
* hardware failure

obviously if we go with a more advanced display, it would subsume this.

this will probably require some change to the croom model.

dankamongmen, 2025-01-29:
ok i'm thinking a 2" TFT LCD ideally with touch capacity wil fly BOM- and implmenetation-wise, and really turn up the tone of our trap.

it ought be on the bottom, on the same side as the antenna and intake fan, as that's the one side we're guaranteed not to be up against a wall (if people are doing things properly). i guess the exhaust side would also work, but that's much farther away from the pcb.

the ST7789V is proven out with eight wires. of those, two are VCC and GND straight off (it's 3.3V). then you've got mandatory SDA and SCL. BL (backlight) can possibly go to VCC, but we might want to control it. CS/DC/RST round out the tank. we've definitely got 5 GPIOs available in the southeast corner of the ESP32-C6, so this seems pretty doable. maybe a 2x4 JST connector?

dankamongmen, 2025-01-29:
st7789v is 320 x 240 with 262k colors. it does not generally include any kind of input interface though hrmmm. a rough check suggests you're getting a 2.4" for $5 if you want input. hrmmmm.

dankamongmen, 2025-01-29:
the fan sides are pretty busy. maybe the side opposite the ac intake? though then we pretty much have to have three sides clear, reducing where we can be used.

dankamongmen, 2025-01-29:
though it's not like you *need* this interface for either monitoring or input. but it would be annoying to not have it. then again, are they putting this thing in a tunnel? corner is no good because you don't have airflow through, so you've got to have  B and C clear, so you're probably going to have D

   A
B    C
   D

dankamongmen, 2025-01-29:
alright i'll run a test of `croomlcd.stl` this afternoon.

dankamongmen, 2025-02-26:
so i put the necessary hole into the croom, ran out the necessary five gpios, and sited a 2x4 JST connector.

but the LCD adds a good bit to our BOM. and even more if we want one with touch input. hrmmmmmmmm.

dankamongmen, 2025-03-14:
https://www.amazon.com/dp/B0CMGF4Q68 i picked up a 2.8" 240x320x65536 IPS TFT with capacitive touchscreen, where everything can run over SPI, for $17. surely we can get it much more cheaply from china. this looks pretty decent, and even includes the FPC cable; we'd need a 14-pin FPC connector on the PCB.

dankamongmen, 2025-03-14:
https://github.com/martinberlin/FT6X36-IDF ought drive the touch, though it's using I2C and i think we'll want SPI (but i2c ought work as well, if it doesn't make the bus too long).

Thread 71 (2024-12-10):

run antenna out of croom

dankamongmen, 2024-12-10:
experimentation has revealed that we lose a lot of connectivity due to the walls of the croom. i've ordered some ESP32-S3-WROOM-U1 models, which allow (and indeed require) an external u.fl antenna. we'll need to run this antenna out of the croom, and mount it somehow. we probably need choose an antenna before designing this.

dankamongmen, 2024-12-14:
https://www.aliexpress.us/item/3256807262687553.html i picked up a pack of ten of these RP-SMA -> U.FL antennae. The SMA connector is 2.5cm long and looks to be 6.35mm in diameter.

dankamongmen, 2024-12-14:
added. it's above and to the left of the fan hole.

Closed 2024-12-14.

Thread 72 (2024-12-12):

eliminate coupling

dankamongmen, 2024-12-12:
I realized last night how we can eliminate the coupling, retaining only the platform and sheath. Instead of the sheath being an extrusion enclosing the entirety of the rotor, we can just have a hole in the base transfixed by the rotor. We could generalize this to cover the entirety of the rotor, but I see no advantage to it.

So instead of

```
   ||
   ||
   ||
---  ---
```

we'll have

```
|---  ---|
|---  ---|
|        |
|        |
|        |
```

where the sheath runs down the length of the motor itself. this eliminates the loose binding between coupling and sheath, yet remains easy to print. big win!

dankamongmen, 2024-12-12:
so the mechanics of this would be:

* cut rotor sheath to minimum height necessary
* enlarge motor sheath to full width of motor, with rotor sheath in its center
** this could be either a cone or cylinder, subject to printing requirements
* cut top rim off of cupola
* merge cupola onto motor sheath
** this provides a cylindrical wrap around the top of the motor, plus the bottom rim necessary for the platform

the platform should remain exactly as it is.

dankamongmen, 2024-12-12:
i've got a prototype weighing in at 8.72g using Bambu Clear Black PC...printing it now

Closed 2024-12-12.

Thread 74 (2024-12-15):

use EMC2302 fan controller IC

dankamongmen, 2024-12-15:
right now we have an ad hoc pair of 4-pin fan management circuits using two resistors and a capacitor for each fan. a 3.3V line is required, as are two GPIOs (again, per fan).

instead, if we use the EMC2302, we only need to run the tach and pwm connections to this IC. a pair of SMBus lines then handle tach+pwm for both fans, requiring only two GPIOs (and we'd be using those anyway for the NAU7802).

first, update the schematic and PCB, and make sure this is going to work routing-wise. once that's proved out, modify our code. probably best to do this in a branch.

dankamongmen, 2024-12-15:
note that we still need a pullup resistor on both tach lines to 3.3V, presumably still 1Kohm.

dankamongmen, 2024-12-29:
i wrote a driver, and we are now using it. haven't been able to test yet -- need to mount an EMC2302 on a SMT->DIP bridge. but it ought work.

Closed 2024-12-29.

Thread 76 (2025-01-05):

feed fan tachs from 12V

dankamongmen, 2025-01-05:
feeding the fan tachs from the 12V line would allow us to clean up the PCB a decent bit, and shouldn't be a problem now that we're using the EMC2302 which is 12V safe. if we do this, we'll want a different resistor between the feed and the pin -- 2.4k to keep us under the 5mA limit.

dankamongmen, 2025-01-05:
nevermind; i checked the EMC2302 datasheet and it can only handle up to 5V on the tachometer inputs, which benefits us not at all.

Closed 2025-01-05.

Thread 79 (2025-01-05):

need properly set GPIO8/GPIO9 strappings

dankamongmen, 2025-01-05:
from the ESP32-C6-MINI datasheet (https://www.espressif.com/sites/default/files/documentation/esp32-c6-mini-1_mini-1u_datasheet_en.pdf)

> GPIO8 and GPIO9 control the boot mode after the reset is released.

| Boot Mode | GPIO8 | GPIO9|
|---------|-------|-------|
|Default Configuration | – (Floating)  |1 (Pull-up)|
|SPI Boot (default) |  Any value | 1|
|Download Boot | 1|  0|
|Invalid combination | 0| 0|

we've got a pullup on GPIO8 and nothing on GPIO9. that looks like it's going to be either SPI boot (if GPIO9 floats high) or Download boot (if GPIO9 floats low). we either want to be able to control it, or always have the same behavior. for now, i think moving the pullup to GPIO9 is sufficient. maybe put a pulldown on GPIO8, but it's not necessary (high on GPIO9 will always do an SPI boot).

dankamongmen, 2025-01-05:
moved the pullup to GPIO9, made GPIO8 a nonconnect. updated schematics, updated PCB.

Closed 2025-01-05.

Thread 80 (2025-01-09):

need a way to write code over UART

dankamongmen, 2025-01-09:
right now we always have GPIO8 bootstrapped high and GPIO9 bootstrapped low. in order to write code to the ESP32-C6-MINI-U1 over UART, we need engage the bootloader by bringing GPIO9 high. add a button which allows GPIO9 to be brought high when held. i don't think we need any code changes, just hardware.

BFE-1020 looks like a good button for our needs. we want normally-open for lower power consumption.

dankamongmen, 2025-01-09:
this was added in bc8f903

Closed 2025-01-09.

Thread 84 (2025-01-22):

remove emc2302 from electronics

dankamongmen, 2025-01-22:
We moved to the EMC2302 because it allowed us to eliminate four wires, riding over the already-allocated I2C lines. Unfortunately, it's nearly impossible to hand-solder, and expensive (more than a dollar per board). Eliminate it, moving back to passive components. This will trade the EMC2302 for two resistors and two capacitors, and require four pins.

dankamongmen, 2025-01-22:
schematics and pcb are updated; we need to update the firmware. it should be possible to just restore some old code (interrupt handler and PWM stuff).

dankamongmen, 2025-01-23:
i've updated the firmware as necessary. emc2302 is gone.

Closed 2025-01-23.

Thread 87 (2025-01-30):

ponder switch to discrete SSR

dankamongmen, 2025-01-30:
right now we've got the triac + optoisolator for about $2 of BOM but $20 of annoyance. they mean AC is on our board. they mean we have to handle ~5A on our board. they make the board substantially larger and lock a lot of territory up. they have regulatory issues.

if we got rid of that section and used a discrete SSR, we eliminate a lot of the stupidity, though it'll be a bit more expensive (figure ~$3). we'll almost certainly need drive the SSR with a 12V MOSFET; our 3.3V isn't generally going to cut it. we'd also need update the croom model to house the SSR, which we'd need select and test. the SSR ought be just as robust as the triac, AFAIK.

we'd probably want to keep the SSR low in the croom, and just run wires up to the heating element, just like we're doing now. check the heat response curve, but smart money says it works better when it's cooler. we'll need non-negligible AWG to carry those amps up, AWG20 or so.

dankamongmen, 2025-01-30:
also, this makes internationalization much easier, as the SSR probably handles 100-300V, whereas the triac likely eats shit well into that range.

dankamongmen, 2025-02-05:
i don't like it. everything i read says it's essentially impossible to get non-counterfeit SSRs. we'd need change up our model. i think what we have is fine.

Closed 2025-02-05.

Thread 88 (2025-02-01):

move 5v buck converter to skyboard

dankamongmen, 2025-02-01:
why are we doing the 5v conversion on the main board, when we only want it up top? it's more efficient to move that as 12v anyway, and it ought be much better for noise. move the 5v buck converter onto the roofboard.

and let's go ahead and lock things down there: i think we're going to use the two throughhole components. we certainly are for the thermometer. if the hall sensor can detect through the floor, we'll use the smd one. otherwise, throughhole for that as well. go ahead and print it onto the PCB, and let's figure out how to do a v-cut in kicad.

dankamongmen, 2025-02-01:
alright, we've now got the microboard integrated into the main PCB, with cuts to support easy breakout. we've moved up the 5v converter. we went with the throughole thermometer and the SMD hall sensor. we'll need test that.

Closed 2025-02-01.

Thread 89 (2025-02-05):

round corners on bottom of croom

dankamongmen, 2025-02-05:
we see too much warping on the corners of the croom. to boost print viability, round up those corners.

dankamongmen, 2025-02-05:
i've cut some pyramids out from the four corners, which ought help out a good bit, and looks cool imho. i need to figure out how to seal the holes, though.

dankamongmen, 2025-02-06:
definitely didn't solve the issue entirely, though. ugh. and we need perfect the fills in the corners, which are currently ad hoc and messy.

dankamongmen, 2025-02-07:
something like this is what we want, using BOSL2:

```
include <BOSL2/std.scad>
prismoid(size1=[50,50], size2=[40,40], h=20, rounding1 = 25, rounding2 = 1);
```

dankamongmen, 2025-02-07:
i do believe we've just about got it

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

dankamongmen, 2025-02-07:
we're admittedly still on layer 1, but this looks like easily the best croom we've ever printed, a big step forward. huzzah!

dankamongmen, 2025-02-07:
i went in and tightened the bottom up another 10mm, as far as she'll go. this cut another 4% off material. at layer 2 of the first print, and we're looking inspired. perfect bottom layer. not a hint of warp nor rise. i think the croom is *done*.

Closed 2025-02-07.

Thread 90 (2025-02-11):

change models to accommodate 80mm load cells

dankamongmen, 2025-02-11:
It looks like the load cells we'll be ordering in bulk are half a centimeter longer, with different hole spacing:

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

we'll need adapt croom and the load cell coupling.

dankamongmen, 2025-02-11:
i updated `loadcelll` to be 80 rather than 76, and moved the croom's mount. still need to adapt the mounting holes on both croom and coupling.

dankamongmen, 2025-02-11:
just need get the coupling now

dankamongmen, 2025-02-11:
we're good!

Closed 2025-02-11.

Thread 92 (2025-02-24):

replace mounting holes in hotbox floor with mounting points

dankamongmen, 2025-02-24:
rather than putting four holes into the floor of the hotbox, and mounting the heater flush with the floor, let's put in a few short mounting posts, and raise it 1mm. this ought help avoid print failures.

dankamongmen, 2025-02-26:
note that we'd still need nuts to secure the PCB/heater/etc, and that this won't work for the AC adapter.

dankamongmen, 2025-02-28:
ok, got all three of them. let's test this out.

Closed 2025-02-28.

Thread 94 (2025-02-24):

more robust access control

dankamongmen, 2025-02-24:
we don't have any authentication on the webserver/mqtt. we need to either:

* add such authentication (making it optional), or
* once the network is set up, lock it so that it can't be changed without a physical touch of the factory reset (see #69 ). this would include disabling network-based factory reset.

i think the first option might be better, even if it's annoying, because there's nothing special about the network configuration vis-a-vis say turning off your drying operation (so long as you can get to the factory reset). but that doesn't lock down mqtt.

maybe we need the following policy matrix:

* orthogonal to everything: specify VLAN (#93)
  * ideally we could hang out on different VLANs for MQTT/HTTP, but that's not important imho (would require two IPs, and we'd probably want to support two different WLANs in this case anyway)
* allow the user to select one of: no mqtt, mqtt reporting only, full mqtt
  * default to no mqtt, since we need to get the broker configured
  * if we do mdns-based mqtt discovery, default to mqtt reporting only
* allow the user to select one of: no http, http(s) reporting only, full http(s)
  * default to full http(s)
  * maybe support IP zeroconf?
* allow the user to select one of: no bluetooth, bluetooth reporting only, full bluetooth, fullbluetooth-unless-we-have-ip
  * bluetooth is on at startup
  * default to fullbluetooth-unless-we-have-ip
    * this mode defaults to reporting-only, but if an IP cannot be acquired, goes to full bluetooth (and back to reporting-only if it gets an IP)
    * more complex than anything else here, questionable
* if http(s) is enabled, allow one user+password to be configured
  * preserve them even if the authentication is disabled, in case it is turned back on

so this supports, among other setups:
* everything is open
* on a VLAN, completely open. if the network changes out from under us, we can reconfigure with bluetooth
* on a VLAN, open save bluetooth
* mqtt is open, http(s) is open, no bluetooth (recommended for minimum complexity)
* mqtt is r/o, http(s) requires logging in, bluetooth is r/o
* mqtt is r/o, http(s) requires logging in, no bluetooth (recommended)

if mqtt is open it doesn't make much sense for http(s) not to be open and vice versa IMHO. bluetooth is different due to the proximity requirements (though given that we're WLAN-only, not so different in truth). i think bluetooth ought be off most of the time, since you can factory reset physically, but the factory reset does kill your other configuration elements. ideally you could just open bluetooth with a physical interaction, allowing you to reconfigure your network without losing other config, hrmmm.

i think allowing mqtt to be r/o and adding authentication + HTTPS (self-signed cert, bleh) are the most critical elements here. also at least simple disabling of bluetooth after setup (i kinda like the idea of making bluetooth open only on a physical interaction...)

dankamongmen, 2025-02-26:
we're not doing anything regarding VLANs. they don't make sense for wireless networks, and aren't supported by ESP-IDF anyway.

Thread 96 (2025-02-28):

eliminate joining bolts between cold and hot chambers

dankamongmen, 2025-02-28:
i'd prefer to use a clasp or screw-in method to connect these two pieces. it would allow us to cut down their material a good bit (we'll just need the central cylinder, flattened a bit on the sides so we can mount fans) and allows them to be assembled more quickly.

ideally, the top of the croom would be the same as the bottom. from there the rest seems pretty obvious.

dankamongmen, 2025-03-01:
this is going on in the `dankamongmen/midjoin` branch.

dankamongmen, 2025-03-01:
i'm thinking the way to do this is with some cantilevers sticking up and out from the croom on all four sides. they'll bite into grooves in all four sides of the bottom of the hotbox. that way the screwing motion of the top won't affect it. let's see how that goes.

dankamongmen, 2025-03-01:
ok, that first attempt was a miserable failure. i'm thinking maybe an annular snap-fit?

dankamongmen, 2025-03-02:
i tested a circular friction fit, and it worked much better...but still not well enough. i think the thing to do is either:
* a series of locks (see https://fab.cba.mit.edu/classes/S62.12/people/vernelle.noel/Plastic_Snap_fit_design.pdf p20 lower right), or
* a true annular snapfit, with the bulge on the croom

dankamongmen, 2025-03-02:
first attempt at annular snapfit

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

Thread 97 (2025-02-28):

don't run trace between pins of miniboard connector

dankamongmen, 2025-02-28:
we currently run the 3.3V rail between two pins on the miniboard connector (see picture).

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

this probably isn't going to fly with JLCPCB tolerances. work out a topology that doesn't need to do this, if possible. if not possible, we might have to look at other options.

dankamongmen, 2025-02-28:
i'm pretty sure we can eliminate this if we use a voltage divider in front of one of the fan tachometers, instead of supplying it from the 3.3V rail directly. and i'm pretty sure we can't otherwise.

dankamongmen, 2025-02-28:
yeah this is looking doable

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

dankamongmen, 2025-02-28:
hrmm except how do we get to the optoisolator/triac with this? =[ unless we moved it away from the corner, between the MCU and the 3.3V rail...ick

dankamongmen, 2025-03-02:
ooooh, we do have a breakout path, between the upper fan hookup and the NAU!

dankamongmen, 2025-03-02:
ooooh, not quite: the 3.3V connection between R1 and J1 kills that.

if we moved J1 inside of the MOSFET, and ran 3.3V to it from the existing 12V stepdown used for J2, that works though? it breaks the 3.3V connection at the cost of a little waste heat (5ma @ 12V maximum for the tachometer open collector, 60mW maximum). let's do it.

dankamongmen, 2025-03-02:
yeah, that gets it.

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

dankamongmen, 2025-03-02:
this is indeed looking cleaner. we need to pump up the trace widths.

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

dankamongmen, 2025-03-04:
ok, this is now resolved in the `dankamongmen/midjoin` branch, which i will merge today.

Closed 2025-03-04.

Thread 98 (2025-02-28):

thread top of mounts to securely accept locknuts

dankamongmen, 2025-02-28:
We'll be using a 5mm locknut on each mounting rod. Keep the bottom of it unthreaded, but thread the top 5mm. I'm pretty sure `threaded.scad` has a part for exactly this usage case.

dankamongmen, 2025-02-28:
yeah it looks like `RodStart` or `RodEnd` will work.

dankamongmen, 2025-02-28:
we want `RodStart`, as it's the one with external threads.

dankamongmen, 2025-02-28:
all done!

Closed 2025-02-28.

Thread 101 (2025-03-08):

investigate using magnets for top+hotbox

dankamongmen, 2025-03-08:
Screwing together the hotbox and top works, and holds it fast, but is annoying -- you have to hold the hotbox+croom assembly immobile. It also looks kinda crappy. Investigate using magnets instead. We'd likely need a minimum of two in both the hotbox and top, and more likely four. If this works out, we could use a screwfit for the croom+hotbox attachment, which would be better than the current frictionfit studs+clips (and since users oughtn't be messing with this, it doesn't matter how it looks).

If we can't get this working, though, the current implementation suffices.

dankamongmen, 2025-03-08:
i don't really see anywhere to put magnets in the ceiling of the hotbox, though. keep this idea cooking, but i don't think it's going to fly =\.

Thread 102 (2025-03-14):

add port for PTFE connector in hotbox

dankamongmen, 2025-03-14:
If we want to print from the dryer (necessary for a closed drying+printing cycle), we need a way to feed the filament out of the hotbox.  we'll want a PTFE connector in there:

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

apparently the bambu connector, good for 4mm OD ptfe tubes, is a 7.9mm head and a M5 screw of 5mm length.

we'll either want to ship a PTFE connector with the dryer, or print a plug (possibly TPU?) and include that.

dankamongmen, 2025-03-14:
with the way our chamber is designed, we'll want this on a corner rather than a face. put it right through one of the corner cutaways, at middle height.

dankamongmen, 2025-03-14:
alright, we now have an M6 going through the front left cutaway:

```scad
module ptfeconn(){
	translate([-spoold / 2 / sqrt(2), -spoold / 2 / sqrt(2), wallz + totalz / 2 + 3]){
		rotate([0, 0, -45]){
			rotate([90, 0, 0]){
				ScrewThread(6, 15);
			}
		}
	}
}
```

let's try it out

dankamongmen, 2025-03-18:
i think this can be improved. we also might want to fit the P4-M10 rather than the P4-M6

dankamongmen, 2025-03-19:
doesn't quite fit when printed in nylon GF...

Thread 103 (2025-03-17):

add connectors to corner areas for croom+hotbox

dankamongmen, 2025-03-17:
we've got a pretty solid setup now with the internal friction fits for the croom+hotbox mating, but with the removal of those on the intake side, i'm a bit worried about the back. there appears to be room for a curving friction fit around each internal corner, and i suggest we use all four. it's a nontrivial but certainly plausible shape to model.

dankamongmen, 2025-03-17:
we can do it much more simply with a chord. we'll need support from underneath, but still, that's pretty trivial.

and if we're gonna do that, they can be the same shapes as our existing plugs/connectors, w00t.

so eight of them around the two. let's start with 40mm x and 40mm y offset from the corner. we want them minimally away from the wall, since we'll need put in a bartizan essentially on the croom.

dankamongmen, 2025-03-17:
ok i think i got it knocked out, testing now...

dankamongmen, 2025-03-18:
looks good! i removed the last remaining set of external clips, as they were prone to breaking off, looked like shit, and were no longer contributing noticeable binding.

Closed 2025-03-18.

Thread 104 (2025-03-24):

nau7802 not being detected on v2.0.0 pcb

dankamongmen, 2025-03-24:
i loaded v2.1.0 onto a 2.0.0 pcb and got it up on serial. we do not appear to be detecting the NAU7802 over i2c:

```
--- Waiting for the device to reconnect..............
using curve fitting adc calibration
E (1699) i2c.master: probe device timeout. Please check if xfer_timeout_ms and pull-ups are correctly set up
E (1699) nau: error 263 detecting NAU7802 at 0x2a
```

looking at the nuvoton data sheet p27 (9.4, "16-pin application circuit"), we've got quite a few deviations that i'm unsure of any justification for (see especially looping of REFP/AVDD and absence of I2C pullups).

dankamongmen, 2025-03-24:
let's first build out the v2.0.0 pcb implementation on a breadboard...

dankamongmen, 2025-03-24:
reduced the Cfilter capacitor from 470 to  recommended 330 pF.

dankamongmen, 2025-03-24:
my first attempt at recreating the circuit on a breadboard is failing. could be good, in that it's a software thing. could be bad, in that i might have fucked up the recreation.

dankamongmen, 2025-03-24:
i'm suspecting software. not seeing anythjng on an i2c decoder. let me bring in the oscilloscope...

dankamongmen, 2025-03-24:
the selae sees our pulses

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

dankamongmen, 2025-03-24:
and we're sending them to the correct address (0x2a)...both buses are pulled up.

hrmmm!

i might not get this resolved today, as i'm heading out in an hour.

dankamongmen, 2025-03-26:
i hadn't updated the pins. things work now!

Closed 2025-03-26.

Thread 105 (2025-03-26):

validate pcb v2.0.0

dankamongmen, 2025-03-26:
they've arrived, assembled, from JLCPCB. verify each component.

[x] working 12V -> 3.3V stepdown
[x] esp32 programmable via uart
[ ] upper fan (power, tach, pwm)
[ ] lower fan (power, tach, pwm)
[ ] nau7802 (detect, tare, weigh)
[ ] triac
[ ] motor
[ ] bluetooth
[ ] wifi
[ ] LM35 at up to 150C

dankamongmen, 2025-03-26:
verified that both tachs work (when the fan header is soldered properly). i do see a systemic divergence between the two fans, despite being physically equal and receiving the same PWM. perhaps a timing effect? we might want to sample closer to the calculation, or at least lift that divide out...

dankamongmen, 2025-03-26:
yeah it looks like we've got IPEX1/u.FL on the antennas and w.FL/IPEX3 on the ESP32-C6-MINI-U1. fuck! i don't see any reasonably priced adapters. we'd likely need get new RP-SMA-IPEX3/MHF3/w.FL cabled connectors at a minimum. adafruit sells a w.FL antenna but it's $2.25 and half the (speced) gain: https://www.adafruit.com/product/5445

dankamongmen, 2025-03-27:
i'm definitely seeing a lot of tach failures, and am no longer certain it's merely my poor soldering. with that said, i've definitely seen reliable tachs in twain on several boards. it would be good to get a better understanding of our lowpass filter on the tachs, and look at our interrupt handler (do we have glitching set up, etc.)?

dankamongmen, 2025-03-27:
> yeah it looks like we've got IPEX1/u.FL on the antennas and w.FL/IPEX3 on the ESP32-C6-MINI-U1. fuck! i don't see any reasonably priced adapters. we'd likely need get new RP-SMA-IPEX3/MHF3/w.FL cabled connectors at a minimum. adafruit sells a w.FL antenna but it's $2.25 and half the (speced) gain: https://www.adafruit.com/product/5445

i ordered 25 w.FL antennas from adafruit. hopefully between now and when we've sold that many, we can get a cheap adapter.

dankamongmen, 2025-03-27:
also worth noting is that even with the 12V input turned off, if we've got a 3.3V USB->UART adapter hooked up, the fans run. that seems off...

dankamongmen, 2025-04-07:
triac control of heater works!

dankamongmen, 2025-04-13:
so the mosfet configuration is screwed up on pcb2.0.0, but we can fix it.

* continue to hook the motor+ up to the left screw terminal--this is 12V, all good
* the motor- is connected to drain of an IRLZ44N through-hole MOSFET
* the MOSFET's source is connected to the unused 4x2 connector's GND pin
* the MOSFET's gate is connected to a throughhole 330 resistor
* the 330 is connected to a 10K and to a signal pin on the 4x2
* the 10K is connected to GND (pulldown resistor)

this ought work just fine, and i have all these parts.

dankamongmen, 2025-04-13:
> * the 330 is connected to a 10K and to a signal pin on the 4x2
> * the 10K is connected to GND (pulldown resistor)

i think we can do without the 10K if we use the ESP32's pullup resistor (there might be a very short period of on when the ESP32 is initializaing)...

dankamongmen, 2025-04-19:
experiments with the pcb 2.0.0 load cell have been negative thus far. i'm validating the 2.2.0 design on breadboard, and will then take a closer look at the (different) 2.0.0 design. it has some problems: for one, we route 3.3V everywhere rather than using the LDO output, especially to E- (possibly A-, either way a problem). so that might fail those boards. in which case we no longer need to support pcb2.0.0 hardware model, kinda tempting heh.

dankamongmen, 2025-04-21:
the load cell issues i've been seeing for several days might come down to shitty wiring. i've validated things with an old load cell, a sparkfun nau7802 board, and the reference software. before i recut the wires, this known-good setup was failing the same way as our implementation. i'm now verifying that our pcb works. ugh.

i think we ought shift from a screw to a spring terminal either way. i've ordered 50.

dankamongmen, 2025-04-21:
with the current setup, we get almost complete linearity using a 100g and 200g test mass and 32x gain:

```
> 17.232597 - 10.761321
6.471276
> (17.232597 - 10.761321) / 2
3.235638
> 13.995469 - 10.761321
3.234148
```

that's a 0.0323148 change per gram, using scaled input at 5000. using unscaled input we get similar results:

```
> 46922.000000 - 36060.000000
10862
> 57770.000000 - 36060.000000
21710
> (57770.000000 - 36060.000000) / 2
10855
>
```

with the convenient aspect that we get a diff ~10K when changing 100g, suggesting about 0.01 deltas. a credit card generated a difference of 409, very reasonable. this is looking good! not sure how constant any of this is across load cells.

dankamongmen, 2025-04-21:
with pga bypassed, we get similar linearity, though of course over a much smaller range (1424 to 2093 for 200g, with 100g at 1755, a delta per 3.331g. as expected, the credit card test is significantly less accurate at this gain level.

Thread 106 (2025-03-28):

move antenna hole to opposite side of fan inlet

dankamongmen, 2025-03-28:
move the antenna hole from the left side to the right side of the "back" of the dryer, as that's where the ESP32 is.

Closed 2025-03-28.

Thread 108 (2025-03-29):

change A+ feed to load cell

dankamongmen, 2025-03-29:
check out this diagram from p27 of the r1.7 NAU7802 datasheet:

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

we currently have 3.3v going directly into A+, REFP, and AVDD. i think we want to make them their own circuit.

this might require enabling LDO via firmware -- check!

dankamongmen, 2025-03-29:
we probably ought check this against the sparkfun/adafruit schematics as well.

dankamongmen, 2025-03-30:
i've changed things up to connect REFP to AVDD with two capacitors running to ground (1u and 100n). this then drives E+.

A+/A- go to VIN1P/VIN1N respectively (with associated passive components).

this brings us inline with the schematic, and also the [adafruit design](https://cdn-learn.adafruit.com/assets/assets/000/111/945/original/adafruit_products_schem.png?1653414816). i definitely think we need test, though.

dankamongmen, 2025-03-30:
we might need to set `PU_CTRL`:`AVDSS` to 1, to select the internal LDO. we're otherwise using the AVSS input, which is wired to REFP.

dankamongmen, 2025-03-30:
i don't read a voltage on either AVDD or REFP with the current code. i think we definitely want to enable the LDO explicitly.

dankamongmen, 2025-03-30:
ok, i'm reading voltage from the LDO pin now, and it's as expected (well, a bit high -- i'm requesting 3.3 and getting 3.5, but that's fine. the next level up is 3.6).

Closed 2025-03-30.

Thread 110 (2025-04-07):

support multiple dryers on a single MQTT broker

dankamongmen, 2025-04-07:
currently, we construct our channel names using `DEVICE`, which is just `hohlraum`. multiple clients cannot differentiate the target of a configuration directive. they probably can't even log in simultaneously.

`DEVICE` has the advantage of being a compile-time constant, facilitating easy string definition. we'll have to make the channel dynamic to support this.

i don't see many people owning multiple dryers early on, and you can still manage them through their web pages. so this isn't terribly important at the moment.

dankamongmen, 2025-04-07:
correction: they use `CLIENTID`, which is currently `#define`d to `DEVICE VERSION`.

dankamongmen, 2025-04-07:
this relies on #107.

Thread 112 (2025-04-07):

kill voltage divider for lower fan

dankamongmen, 2025-04-07:
now that we're only taking 3.3V up to the miniboard, we can rearrange things so that both 12V and 3.3V get to the lower fan hookup, eliminating the need for the voltage divider from the 12V line to LTach. make it so. this should be done for the 2.2.0 PCB.

dankamongmen, 2025-04-08:
done. we eliminated one resistor entirely, and the other is now a 680 instead of 6.8k, which ought eliminate a component charge from JLCPCB.

Closed 2025-04-08.

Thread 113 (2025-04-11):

need a clip to hold IEC plug into croom

dankamongmen, 2025-04-11:
when we shove the IEC plug into the croom, it's currently only held via friction. when unplugging the unit, sometimes it gets pulled out along with the plug. we need a very small plug, corresponding to 'A' in this diagram:

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

dankamongmen, 2025-04-11:
it looks like we want 1mm depth and 1.5mm height.

dankamongmen, 2025-04-11:
alright, models v2.2.1 have the clips. let's test it out.

Closed 2025-04-11.

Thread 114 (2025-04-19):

move load to end of load cell

dankamongmen, 2025-04-19:
i think we've got the load suboptimally placed on the load cell. it's currently in the center, right atop the glued portion. but atop the glued portion is bad (can damage the component), and it appears we want the load on the end of the cell. see:

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

*but* we still need the load to be centered relative to the chamber. so we need to move the load cell mount towards the side, and redesign the lower coupling to screw directly into the far end. the centering needs to be fairly precise.

dankamongmen, 2025-04-19:
ok, we have the cutout in the center of the lower coupling, so we don't need to worry about pressure on the sensor--we ought be fine there.

dankamongmen, 2025-04-19:
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

yeah we want the load on the end, though.

dankamongmen, 2025-04-21:
i've updated the croom to offset the loadcellmount. we now need redesign the lower coupling, which ought be a matter of simplifying it.

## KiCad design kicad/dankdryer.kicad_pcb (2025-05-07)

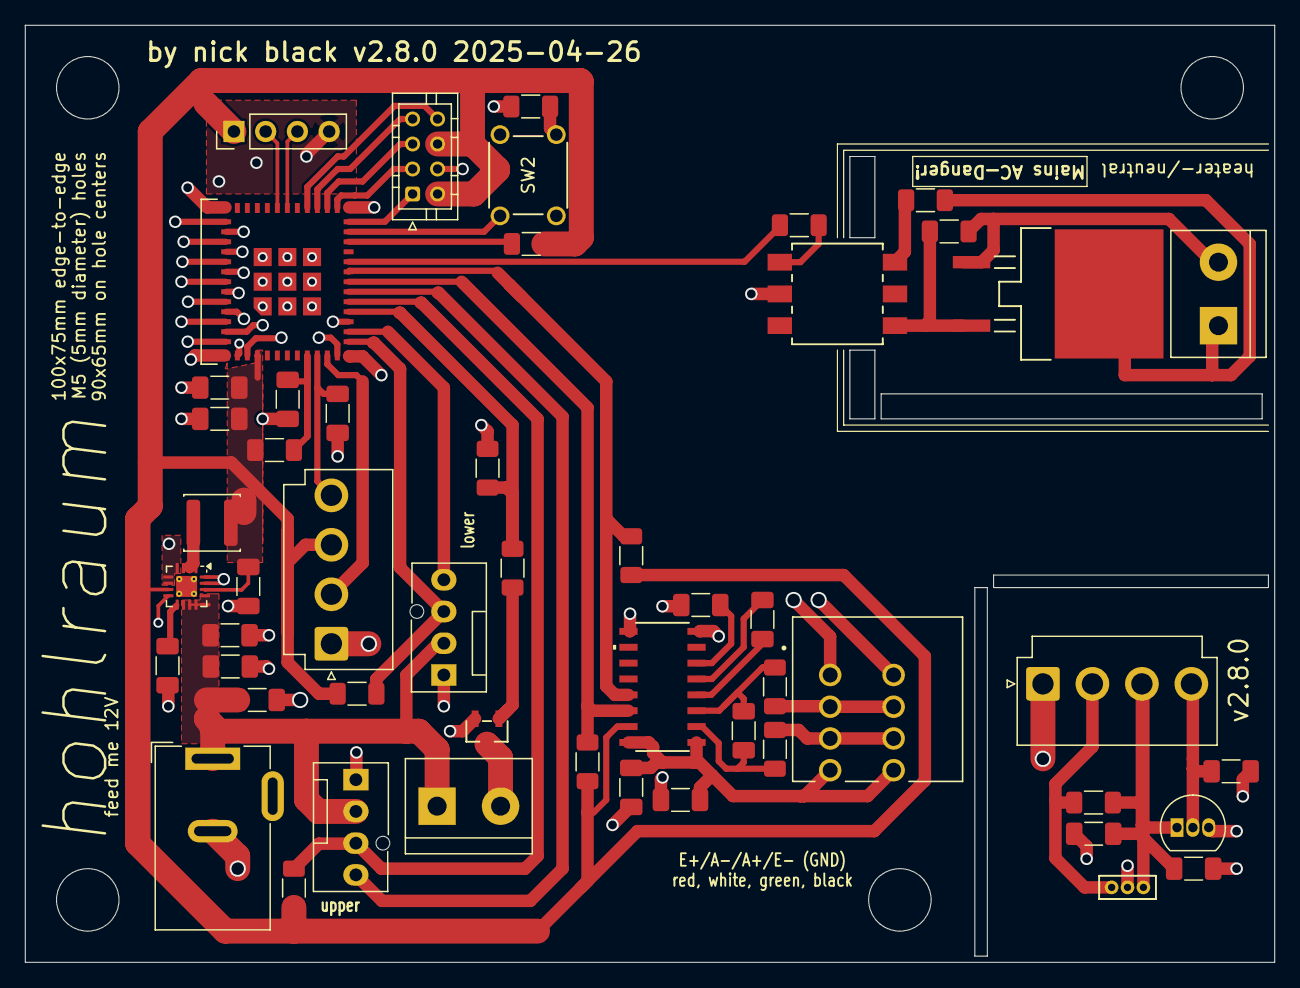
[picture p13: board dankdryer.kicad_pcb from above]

Board: 2 copper layers, 100.0 x 75.0 mm, 52 parts (0 on the bottom side), 44 nets.

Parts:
C1, C14, C19: 10u; C_1206_3216Metric_Pad1.33x1.80mm_HandSolder
C2, C3, C5, C8, C9, C20: 100n; C_1206_3216Metric_Pad1.33x1.80mm_HandSolder
C4: 10n; C_1206_3216Metric_Pad1.33x1.80mm_HandSolder
C6, C21: 22u; C_1206_3216Metric_Pad1.33x1.80mm_HandSolder
C7: 3.3n; C_1206_3216Metric_Pad1.33x1.80mm_HandSolder
C10, C12, C17: 1u; C_1206_3216Metric_Pad1.33x1.80mm_HandSolder
C11: 330p; C_1206_3216Metric_Pad1.33x1.80mm_HandSolder
D1: T1210-800G-TR
J1: 1-2834016-4; TE_1-2834016-4
J2: to microboard; JST_VH_B4P-VH-B_1x04_P3.96mm_Vertical
J3: to baseboard; JST_VH_B4P-VH-B_1x04_P3.96mm_Vertical
J4, J8: ScrewX2; TerminalBlock_bornier-2_P5.08mm
J6: LCD; JST_PHD_B8B-PHDSS_2x04_P2.00mm_Vertical
J7, J10: HeaderX4; FanPinHeader_1x04_P2.54mm_Vertical
J9: UART; PinHeader_1x04_P2.54mm_Vertical
J13: barreljack; BarrelJack_Wuerth_6941xx301002
L1: 2.2u; L_Sunlord_SWPA4030S
OC1: MOC3063SM; MOC306XS_LTO
Q1: AH3712-P-B; TRANS_AH3712-P-B_DIO
Q2: IRLML2502TRPbF; IRLML2502TRPBF
R1, R5: 680; R_1206_3216Metric_Pad1.30x1.75mm_HandSolder
R2, R12: 330; R_1206_3216Metric_Pad1.30x1.75mm_HandSolder
R3: 100; R_1206_3216Metric_Pad1.30x1.75mm_HandSolder
R4: 390; R_1206_3216Metric_Pad1.30x1.75mm_HandSolder
R6, R8: 2.2k; R_1206_3216Metric_Pad1.30x1.75mm_HandSolder
R7, R13, R15, R20: 10k; R_1206_3216Metric_Pad1.30x1.75mm_HandSolder
R10, R11: 47; R_1206_3216Metric_Pad1.30x1.75mm_HandSolder
R14: 3.3k; R_1206_3216Metric_Pad1.30x1.75mm_HandSolder
SW2: boot; SW_B3F-1000_OMR
U3: NAU7802SGI; SOI16_NAU7802SGI_NUV
U4: TPS62132RGTR; VQFN-16-1EP_3x3mm_P0.5mm_EP1.68x1.68mm_ThermalVias
U5: LMT87LPM; TO-92_Inline
U6: ESP32-C6-MINI-1U; ESP32-C6-MINI-1U-H4

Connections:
+3.3V: C3.1, C6.2, C21.1, J2.3, J6.2, J6.6, J9.1, L1.2, R1.1, R5.1, R6.1, R8.1, R13.1, R15.1, U3.15 (DVDD), U4.7 (FSW), U4.14 (VOS), U6.3 (3V3)
+3.3Vmicro: C4.2, C19.2, J3.3, Q1.1 (VDD), R20.1, U5.1 (+V_{S})
+12V: C1.1, C2.2, C14.1, J7.2, J8.1, J10.2, J13.1, U4.10 (AVIN), U4.11 (PVIN), U4.12 (PVIN__1), U4.13 (EN)
/ACNeutral: D1.1 (A1), J4.2, R4.2
/BootDown: R15.2, U6.22 (IO8)
/BootSPI: SW2.1, U6.23 (IO9)
/Hall: J2.2, U6.10 (IO5)
/HeaterNeutral: D1.3 (A2), J4.1, R3.2
/LPWM: J10.4, U6.13 (IO1)
/LTach: J10.3, R5.2, U6.12 (IO0)
/Microboard/HallMicro: J3.2, Q1.3 (OUTPUT), R20.2
/Microboard/ThermMicro: C17.2, J3.4, U5.2 (V_{OUT})
/Motor: R7.1, R12.1, U6.15 (IO6)
/RXD0: J9.3, U6.30 (RXD0)
/SCL: R6.2, U3.13 (SCLK), U6.19 (IO14)
/SDA: R8.2, U3.14 (SDIO), U6.18 (IO13)
/SSRControl: R2.2, U6.20 (IO15)
/TXD0: J9.2, U6.31 (TXD0)
/Therm: C20.1, J2.4, U6.9 (IO4)
/UPWM: J7.4, U6.17 (IO12)
/UTach: J7.3, R1.2, U6.16 (IO7)
A+: J1.2_1 (2), J1.2_2 (2__1), R11.1
A-: J1.3_1 (3), J1.3_2 (3__1), R10.1
E+: C5.1, C12.1, J1.4_1 (4), J1.4_2 (4__1), U3.1 (REFP), U3.16 (AVDD/LDO)
GND: C1.2, C2.1, C3.2, C4.1, C5.2, C6.1, C7.2, C8.2, C10.2, C12.2, C14.2, C17.1, C19.1, C20.2, C21.2, J1.1_1 (1), J1.1_2 (1__1), J2.1, J3.1, J6.4, J7.1, J9.4, J10.1, J13.2, OC1.2 (C), Q1.2 (GND), Q2.2 (S), R7.2, R14.2, U3.8 (AVSS), U3.9 (DVSS), U4.4 (PG), U4.5 (FB), U4.6 (AGND), U4.8 (DEF), U4.15 (PGND), U4.16 (PGND__1), U4.17 (PGND__2), U5.3 (GND), U6.1 (GND1), U6.2 (GND1), U6.11 (GND1), U6.14 (GND1), U6.36 (GND1), U6.37 (GND1), U6.38 (GND1), U6.39 (GND1), U6.40 (GND1), U6.41 (GND1), U6.42 (GND1), U6.43 (GND1), U6.44 (GND1), U6.45 (GND1), U6.46 (GND1), U6.47 (GND2), U6.48 (GND2), U6.49_1 (GND2), U6.49_2 (GND2), U6.49_3 (GND2), U6.49_4 (GND2), U6.49_5 (GND2), U6.49_6 (GND2), U6.49_7 (GND2), U6.49_8 (GND2), U6.49_9 (GND2), U6.50 (GND2), U6.51 (GND2), U6.52 (GND2), U6.53 (GND2)
LCDCS: J6.8, U6.28 (IO22)
LCDDC: J6.7, U6.27 (IO21)
LCDRst: J6.1, U6.24 (IO18)
LCDSCL: J6.3, U6.25 (IO19)
LCDSDA: J6.5, U6.26 (IO20)
unnamed: D1.2 (G), OC1.4 (MT1), R4.1
unnamed: J8.2, Q2.3 (D)
unnamed: OC1.1 (A), R2.1
unnamed: OC1.6 (MT2), R3.1
unnamed: Q2.1 (G), R12.2
unnamed: R14.1, SW2.4
unnamed: C8.1, U3.6 (VBG)
unnamed: C9.1, R10.2, U3.2 (VIN1N)
unnamed: C9.2, R11.2, U3.3 (VIN1P)
unnamed: C11.1, U3.4 (VIN2N)
unnamed: C11.2, U3.5 (VIN2P)
unnamed: C7.1, U4.9 (SS/TR)
unnamed: L1.1, U4.1 (SW), U4.2 (SW__1), U4.3 (SW__2)
unnamed: C10.1, R13.2, U6.8 (EN)

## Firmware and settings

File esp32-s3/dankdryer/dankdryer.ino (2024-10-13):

// dankdryer firmware
// intended for use on an ESP32-S3-WROOM-1
#define VERSION "0.0.1"
#define DEVICE "dankdryer"
#define CLIENTID DEVICE VERSION
#include "dryer-network.h"
#include <lwip/netif.h>
#include <nvs.h>
#include <mdns.h>
#include <Wire.h>
#include <HX711.h>
#include <esp_wifi.h>
#include <esp_netif.h>
#include <nvs_flash.h>
#include <esp_system.h>
#include <ArduinoJson.h>
#include <mqtt_client.h>
#include <driver/ledc.h>
#include <hal/ledc_types.h>
#include <driver/temperature_sensor.h>

#define FANPWM_BIT_NUM LEDC_TIMER_8_BIT
#define RPMMAX (1u << 14u)

// GPIO numbers (https://docs.espressif.com/projects/esp-idf/en/stable/esp32s3/api-reference/peripherals/gpio.html)
// 0 and 3 are strapping pins
#define MOTOR_PWMPIN GPIO_NUM_4 // motor speed
#define THERM_DATAPIN GPIO_NUM_8 // analog thermometer (input)
#define MOTOR_SBYPIN GPIO_NUM_9  // standby must be taken high to drive motor (output)
#define LOWER_PWMPIN GPIO_NUM_11  // lower chamber fan speed (output)
#define LOWER_TACHPIN GPIO_NUM_12 // lower chamber fan tachometer (input)
#define UPPER_PWMPIN GPIO_NUM_10  // upper chamber fan speed (output)
#define UPPER_TACHPIN GPIO_NUM_13 // upper chamber fan tachometer (input)
#define HX711_SCK GPIO_NUM_17    // DAC clock (i2c)
#define HX711_DT GPIO_NUM_18     // DAC data (i2c)
// 19--20 are used for JTAG (not strictly needed)
// 26--32 are used for pstore qspi flash
// 38 is used for RGB LED
#define MOTOR_1PIN GPIO_NUM_39
// 45 and 46 are strapping pins
#define MOTOR_2PIN GPIO_NUM_48

#define NVS_HANDLE_NAME "pstore"

HX711 Load;
static bool UsePersistentStore; // set true upon successful initialization
static temperature_sensor_handle_t temp;
static const ledc_channel_t LOWER_FANCHAN = LEDC_CHANNEL_0;
static const ledc_channel_t UPPER_FANCHAN = LEDC_CHANNEL_1;
static const ledc_channel_t MOTOR_CHAN = LEDC_CHANNEL_2;
static const ledc_mode_t LEDCMODE = LEDC_LOW_SPEED_MODE; // no high-speed on S3

// defaults, some of which can be configured.
static uint32_t MotorPWM;
static uint32_t LowerPWM = 64;
static uint32_t UpperPWM = 64;
static uint32_t TargetTemp = 80;
static float LoadcellScale = 1.0;
static uint32_t LowerPulses, UpperPulses; // tach signals recorded
static esp_mqtt_client_handle_t MQTTHandle;

typedef struct failure_indication {
  int r, g, b;
} failure_indication;

static enum network_state_e {
  WIFI_INVALID,
  WIFI_CONNECTING,
  NET_CONNECTING,
  MQTT_CONNECTING,
  MQTT_ESTABLISHED,
  NETWORK_STATE_COUNT
} NetworkState;

static bool StartupFailure;
static const failure_indication PreFailure = { RGB_BRIGHTNESS, RGB_BRIGHTNESS, RGB_BRIGHTNESS };
static const failure_indication SystemError = { RGB_BRIGHTNESS, 0, 0 };
static const failure_indication NetworkError = { RGB_BRIGHTNESS, 0, RGB_BRIGHTNESS };
static const failure_indication PostFailure = { 0, 0, 0 };
static const failure_indication NetworkIndications[NETWORK_STATE_COUNT] = {
  { 0, 255, 0 },  // WIFI_INVALID
  { 0, 192, 0 }, // WIFI_CONNECTING
  { 0, 128, 0 }, // NET_CONNECTING
  { 0, 64, 0 },  // MQTT_CONNECTING
  { 0, 0, 0 }    // MQTT_ESTABLISHED
};

static const esp_mqtt_client_config_t MQTTConfig = {
  .broker = {
    .address = {
      .uri = MQTTURI,
    },
  },
  .credentials = {
    .username = MQTTUSER,
    // FIXME set client id, but stir in some per-device data
    .authentication = {
      .password = MQTTPASS,
    },
  },
};

// ---------------------------------------------------------
// needed with 3.0.3, see https://github.com/espressif/arduino-esp32/issues/10084 
// FIXME remove this garbage
extern "C" int lwip_hook_ip6_input(struct pbuf *p, struct netif *inp) __attribute__((weak));
extern "C" int lwip_hook_ip6_input(struct pbuf *p, struct netif *inp) {
  if (ip6_addr_isany_val(inp->ip6_addr[0].u_addr.ip6)) {
    // We don't have an LL address -> eat this packet here, so it won't get accepted on input netif
    pbuf_free(p);
    return 1;
  }
  return 0;
}
// ---------------------------------------------------------

void tach_isr(void* pulsecount){
  auto pc = static_cast<uint32_t*>(pulsecount);
  ++*pc;
}

static inline bool valid_pwm_p(int pwm){
  return pwm >= 0 && pwm <= 255;
}

// precondition: isxdigit(c) is true
byte get_hex(char c){
  if(isdigit(c)){
    return c - '0';
  }
  c = tolower(c);
  return c - 'a' + 10;
}

// FIXME handle base 10 numbers as well (can we use strtoul?)
int extract_pwm(const char* data, size_t dlen){
  if(dlen != 2){
    printf("pwm wasn't 2 characters\n");
    return -1;
  }
  char h = data[0];
  char l = data[1];
  if(!isxdigit(h) || !isxdigit(l)){
    printf("invalid hex character\n");
    return -1;
  }
  byte hb = get_hex(h);
  byte lb = get_hex(l);
  // everything was valid
  int pwm = hb * 16 + lb;
  printf("got pwm value: %d\n", pwm);
  return pwm;
}

// set the desired PWM value
int set_pwm(const ledc_channel_t channel, unsigned pwm){
  if(ledc_set_duty(LEDCMODE, channel, pwm) != ESP_OK){
    fprintf(stderr, "error setting pwm!\n");
    return -1;
  }else if(ledc_update_duty(LEDCMODE, channel) != ESP_OK){
    fprintf(stderr, "error committing pwm!\n");
    return -1;
  }
  printf("set pwm to %u on channel %d\n", pwm, channel);
  return 0;
}

float getAmbient(void){
  float t;
  if(temperature_sensor_get_celsius(temp, &t)){
    fprintf(stderr, "failed acquiring temperature\n");
    return NAN;
  }
  return t;
}

float getWeight(void){
  Load.wait_ready();
  return Load.read_average(5);
}

// the esp32-s3 has a built in temperature sensor
int setup_esp32temp(void){
  temperature_sensor_config_t conf = TEMPERATURE_SENSOR_CONFIG_DEFAULT(-10, 80);
  if(temperature_sensor_install(&conf, &temp) != ESP_OK){
    fprintf(stderr, "failed to set up thermostat\n");
    return -1;
  }
  if(temperature_sensor_enable(temp) != ESP_OK){
    fprintf(stderr, "failed to enable thermostat\n");
    return -1;
  }
  return 0;
}

int init_pstore(void){
  printf("initializing persistent store...\n");
  esp_err_t err = nvs_flash_init();
  if(err == ESP_ERR_NVS_NO_FREE_PAGES || err == ESP_ERR_NVS_NEW_VERSION_FOUND){
    // FIXME LED feedback during erase + init
    printf("erasing flash...\n");
    err = nvs_flash_erase();
    if(err == ESP_OK){
      printf("initializing flash...\n");
      err = nvs_flash_init();
    }
  }
  if(err){
    // FIXME LED feedback
    fprintf(stderr, "failure (%d) initializing nvs!\n", err);
    return -1;
  }
  return 0;
}

// check for an optional record in the nvs handle. if not defined, return 0.
// if defined, load val and return 0. on other errors, return -1.
int nvs_get_opt_u32(nvs_handle_t nh, const char* recname, uint32_t* val){
  esp_err_t err = nvs_get_u32(nh, recname, val);
  if(err == ESP_ERR_NVS_NOT_FOUND){
    printf("no record '%s' in nvs\n", recname);
    return 0;
  }else if(err){
    fprintf(stderr, "failure (%d) reading %s\n", err, recname);
    return -1;
  }
  printf("read configured default %lu from nvs:%s\n", *val, recname);
  return 0;
}

// NVS can't use floats directly. we instead write/read them as strings.
int nvs_get_opt_float(nvs_handle_t nh, const char* recname, float* val){
  char buf[32];
  unsigned blen = sizeof(buf);
  esp_err_t err = nvs_get_str(nh, recname, buf, &blen);
  if(err == ESP_ERR_NVS_NOT_FOUND){
    printf("no record '%s' in nvs\n", recname);
    return 0;
  }else if(err){
    fprintf(stderr, "failure (%s) reading %s\n", esp_err_to_name(err), recname);
    return -1;
  }
  char* bend;
  *val = strtof(buf, &bend);
  if(bend || !*val || isnan(*val)){
    fprintf(stderr, "couldn't convert [%s] to float for nvs:%s\n", buf, recname);
    return -1;
  }
  printf("read configured default %f from nvs:%s\n", *val, recname);
  return 0;
}

// read and update boot count, read configurable defaults from pstore if they
// are present (we do not write defaults to pstore, so we can differentiate
// between defaults and a configured value).
int read_pstore(void){
  nvs_handle_t nvsh;
  esp_err_t err = nvs_open(NVS_HANDLE_NAME, NVS_READWRITE, &nvsh);
  if(err){
    fprintf(stderr, "failure (%d) opening nvs:" NVS_HANDLE_NAME "\n", err);
    return -1;
  }
  uint32_t bootcount;
#define BOOTCOUNT_RECNAME "bootcount"
  err = nvs_get_u32(nvsh, BOOTCOUNT_RECNAME, &bootcount);
  if(err && err != ESP_ERR_NVS_NOT_FOUND){
    fprintf(stderr, "failure (%d) reading " NVS_HANDLE_NAME ":" BOOTCOUNT_RECNAME "\n", err);
    nvs_close(nvsh);
    return -1;
  }
  ++bootcount;
  printf("this is boot #%lu\n", bootcount);
  err = nvs_set_u32(nvsh, BOOTCOUNT_RECNAME, bootcount);
  if(err){
    fprintf(stderr, "failure (%d) writing " NVS_HANDLE_NAME ":" BOOTCOUNT_RECNAME "\n", err);
    nvs_close(nvsh);
    return -1;
  }
#undef BOOTCOUNT_RECNAME
  err = nvs_commit(nvsh);
  if(err){
    fprintf(stderr, "failure (%d) committing nvs:" NVS_HANDLE_NAME "\n", err);
    nvs_close(nvsh);
    return -1;
  }
  nvs_get_opt_u32(nvsh, "targtemp", &TargetTemp);
  nvs_get_opt_u32(nvsh, "upperfanpwm", &UpperPWM);
  nvs_get_opt_u32(nvsh, "lowerfanpwm", &LowerPWM);
  nvs_get_opt_float(nvsh, "loadcellscale", &LoadcellScale);
  // FIXME check any defaults we read and ensure they're sane
  // FIXME need we check for error here?
  nvs_close(nvsh);
  return 0;
}

int initialize_pwm(ledc_channel_t channel, gpio_num_t pin, int freq, ledc_timer_t timer){
  pinMode(pin, OUTPUT);
  ledc_channel_config_t conf;
  memset(&conf, 0, sizeof(conf));
  conf.gpio_num = pin;
  conf.speed_mode = LEDCMODE;
  conf.intr_type = LEDC_INTR_DISABLE;
  conf.timer_sel = timer;
  conf.duty = FANPWM_BIT_NUM;
  conf.channel = channel;
  printf("setting up pin %d for %dHz PWM\n", pin, freq);
  if(ledc_channel_config(&conf) != ESP_OK){
    fprintf(stderr, "error (channel config)!\n");
    return -1;
  }
  ledc_timer_config_t ledc_timer;
  memset(&ledc_timer, 0, sizeof(ledc_timer));
  ledc_timer.speed_mode = LEDCMODE;
  ledc_timer.duty_resolution = FANPWM_BIT_NUM;
  ledc_timer.timer_num = timer;
  ledc_timer.freq_hz = freq;
  if(ledc_timer_config(&ledc_timer) != ESP_OK){
    fprintf(stderr, "error (timer config)!\n");
    return -1;
  }
  return 0;
}

int initialize_25k_pwm(ledc_channel_t channel, gpio_num_t pin, ledc_timer_t timer){
  return initialize_pwm(channel, pin, 25000, timer);
}

int gpio_set_input(gpio_num_t pin){
  esp_err_t err;
  if((err = gpio_set_direction(pin, GPIO_MODE_INPUT)) != ESP_OK){
    fprintf(stderr, "failure %d (%s) setting %d to input\n", err, esp_err_to_name(err), pin);
    return -1;
  }
  return 0;
}

int gpio_set_output(gpio_num_t pin){
  esp_err_t err;
  if((err = gpio_set_direction(pin, GPIO_MODE_OUTPUT)) != ESP_OK){
    fprintf(stderr, "failure %d (%s) setting %d to output\n", err, esp_err_to_name(err), pin);
    return -1;
  }
  return 0;
}

int initialize_tach(gpio_num_t pin, uint32_t* arg){
  if(gpio_set_input(pin)){
    return -1;
  }
  attachInterruptArg(pin, tach_isr, arg, FALLING);
  return 0;
}

int setup_fans(gpio_num_t lowerppin, gpio_num_t upperppin,
               gpio_num_t lowertpin, gpio_num_t uppertpin){
  int ret = 0;
  if(initialize_tach(lowertpin, &LowerPulses)){
    ret = -1;
  }
  if(initialize_tach(uppertpin, &UpperPulses)){
    ret = -1;
  }
  // intentional '|'s to avoid short circuiting
  if(gpio_set_output(lowerppin) | gpio_set_output(upperppin)){
    ret = -1;
  }
  initialize_25k_pwm(LOWER_FANCHAN, lowerppin, LEDC_TIMER_1);
  initialize_25k_pwm(UPPER_FANCHAN, upperppin, LEDC_TIMER_2);
  set_pwm(LOWER_FANCHAN, LowerPWM);
  set_pwm(UPPER_FANCHAN, UpperPWM);
  return ret;
}

void set_network_state(network_state_e state){
  // FIXME lock
  NetworkState = state;
  if(state != WIFI_INVALID){ // if invalid, leave any initial failure status up
    if(state < NETWORK_STATE_COUNT){
      set_led(&NetworkIndications[state]);
    }
  }
}

void wifi_event_handler(void* arg, esp_event_base_t base, int32_t id, void* data){
  esp_err_t err;
  if(strcmp(base, WIFI_EVENT)){
    fprintf(stderr, "non-wifi event %s in wifi handler\n", base);
    return;
  }
  if(id == WIFI_EVENT_STA_START || id == WIFI_EVENT_STA_DISCONNECTED){
    set_network_state(WIFI_CONNECTING);
    if((err = esp_wifi_connect()) != ESP_OK){
      fprintf(stderr, "failure (%d %s) connecting to wifi\n", err, esp_err_to_name(err));
    }
  }else if(id == WIFI_EVENT_STA_CONNECTED){
    set_network_state(NET_CONNECTING);
    printf("connected to wifi, looking for ip\n");
    uint16_t aid = 65535u;
    esp_wifi_sta_get_aid(&aid);
    printf("association id: %u\n", aid);
  }else{
    fprintf(stderr, "unknown wifi event %ld\n", id);
  }
}

void ip_event_handler(void* arg, esp_event_base_t base, int32_t id, void* data){
  esp_err_t err;
  if(strcmp(base, IP_EVENT)){
    fprintf(stderr, "non-ip event %s in ip handler\n", base);
    return;
  }
  if(id == IP_EVENT_STA_GOT_IP || id == IP_EVENT_GOT_IP6){
    printf("got network address, connecting to mqtt\n");
    set_network_state(MQTT_CONNECTING);
    if((err = esp_mqtt_client_start(MQTTHandle)) != ESP_OK){
      fprintf(stderr, "failure (%d %s) connecting to mqtt\n", err, esp_err_to_name(err));
    }
  }else{
    fprintf(stderr, "unknown ip event %ld\n", id);
  }
}

#define CCHAN "control/"
#define MPWM_CHANNEL CCHAN DEVICE "/mpwm"
#define LPWM_CHANNEL CCHAN DEVICE "/lpwm"
#define UPWM_CHANNEL CCHAN DEVICE "/upwm"

void handle_mqtt_msg(const esp_mqtt_event_t* e){
  printf("control message [%.*s] [%.*s]\n", e->topic_len, e->topic, e->data_len, e->data);
  if(strncmp(e->topic, MPWM_CHANNEL, e->topic_len) == 0 && e->topic_len == strlen(MPWM_CHANNEL)){
    auto pwm = extract_pwm(e->data, e->data_len);
    if(pwm >= 0){
      MotorPWM = pwm;
      set_motor_pwm();
    }
  }else if(strncmp(e->topic, LPWM_CHANNEL, e->topic_len) == 0 && e->topic_len == strlen(LPWM_CHANNEL)){
    auto pwm = extract_pwm(e->data, e->data_len);
    if(pwm >= 0){
      LowerPWM = pwm;
      set_pwm(LOWER_FANCHAN, LowerPWM);
    }
  }else if(strncmp(e->topic, UPWM_CHANNEL, e->topic_len) == 0 && e->topic_len == strlen(UPWM_CHANNEL)){
    auto pwm = extract_pwm(e->data, e->data_len);
    if(pwm >= 0){
      UpperPWM = pwm;
      set_pwm(UPPER_FANCHAN, UpperPWM);
    }
  }else{
    fprintf(stderr, "unknown topic, ignoring message\n");
  }
}

void mqtt_event_handler(void* arg, esp_event_base_t base, int32_t id, void* data){
  if(id == MQTT_EVENT_CONNECTED){
    printf("connected to mqtt\n");
    set_network_state(MQTT_ESTABLISHED);
    int er;
    if( (er = esp_mqtt_client_subscribe(MQTTHandle, MPWM_CHANNEL, 0)) ){
      fprintf(stderr, "failure %d subscribing to mqtt mpwm topic\n", er);
    }
    if( (er = esp_mqtt_client_subscribe(MQTTHandle, LPWM_CHANNEL, 0)) ){
      fprintf(stderr, "failure %d subscribing to mqtt lpwm topic\n", er);
    }
    if( (er = esp_mqtt_client_subscribe(MQTTHandle, UPWM_CHANNEL, 0)) ){
      fprintf(stderr, "failure %d subscribing to mqtt upwm topic\n", er);
    }
  }else if(id == MQTT_EVENT_DATA){
    handle_mqtt_msg(static_cast<const esp_mqtt_event_t*>(data));
  }else{
    printf("unhandled mqtt event %ld\n", id);
  }
}

int setup_mdns(void){
  esp_err_t err;
  if((err = mdns_init()) != ESP_OK){
    fprintf(stderr, "failure %d (%s) initializing mDNS\n", err, esp_err_to_name(err));
    return -1;
  }
  if((err = mdns_hostname_set(CLIENTID)) != ESP_OK){
    fprintf(stderr, "failure %d (%s) initializing mDNS\n", err, esp_err_to_name(err));
    return -1;
  }
  mdns_instance_name_set("Dire Dryer");
  mdns_service_add(NULL, "_http", "_tcp", 80, NULL, 0);
  mdns_service_instance_name_set("_http", "_tcp", "Dire Dryer webserver");
  return 0;
}

int setup_network(void){
  if((MQTTHandle = esp_mqtt_client_init(&MQTTConfig)) == NULL){
    fprintf(stderr, "couldn't create mqtt client\n");
    return -1;
  }
  const wifi_init_config_t wificfg = WIFI_INIT_CONFIG_DEFAULT();
  esp_err_t err;
  wifi_config_t stacfg = {
    .sta = {
        .ssid = WIFIESSID,
        .password = WIFIPASS,
        .sort_method = WIFI_CONNECT_AP_BY_SECURITY,
        .threshold = {
            .authmode = WIFI_AUTH_WPA2_PSK,
        },
        .sae_pwe_h2e = WPA3_SAE_PWE_HUNT_AND_PECK,
        .sae_h2e_identifier = "",
    },
  };
  if((err = esp_netif_init()) != ESP_OK){
    fprintf(stderr, "failure %d (%s) initializing tcp/ip\n", err, esp_err_to_name(err));
    goto bail;
  }
  if((err = esp_event_loop_create_default()) != ESP_OK){
    fprintf(stderr, "failure %d (%s) creating loop\n", err, esp_err_to_name(err));
    goto bail;
  }
  if(!esp_netif_create_default_wifi_sta()){
    fprintf(stderr, "failure creating default STA\n");
    goto bail;
  }
  if((err = esp_wifi_init(&wificfg)) != ESP_OK){
    fprintf(stderr, "failure %d (%s) initializing wifi\n", err, esp_err_to_name(err));
    goto bail;
  }
  esp_event_handler_instance_t wid;
  if((err = esp_event_handler_instance_register(WIFI_EVENT, ESP_EVENT_ANY_ID, wifi_event_handler, NULL, &wid)) != ESP_OK){
    fprintf(stderr, "failure %d (%s) registering wifi events\n", err, esp_err_to_name(err));
    goto bail;
  }
  esp_event_handler_instance_t ipd;
  if((err = esp_event_handler_instance_register(IP_EVENT, ESP_EVENT_ANY_ID, ip_event_handler, NULL, &ipd)) != ESP_OK){
    fprintf(stderr, "failure %d (%s) registering ip events\n", err, esp_err_to_name(err));
    goto bail;
  }
  if((err = esp_mqtt_client_register_event(MQTTHandle, MQTT_EVENT_CONNECTED, mqtt_event_handler, NULL)) != ESP_OK){
    fprintf(stderr, "failure %d (%s) registering mqtt events\n", err, esp_err_to_name(err));
    goto bail;
  }
  if((err = esp_mqtt_client_register_event(MQTTHandle, MQTT_EVENT_DATA, mqtt_event_handler, NULL)) != ESP_OK){
    fprintf(stderr, "failure %d (%s) registering mqtt events\n", err, esp_err_to_name(err));
    goto bail;
  }
  if((err = esp_wifi_set_mode(WIFI_MODE_STA)) != ESP_OK){
    fprintf(stderr, "failure %d (%s) setting STA mode\n", err, esp_err_to_name(err));
    goto bail;
  }
  if((err = esp_wifi_set_config(WIFI_IF_STA, &stacfg)) != ESP_OK){
    fprintf(stderr, "failure %d (%s) configuring wifi\n", err, esp_err_to_name(err));
    goto bail;
  }
  if((err = esp_wifi_start()) != ESP_OK){
    fprintf(stderr, "failure %d (%s) starting wifi\n", err, esp_err_to_name(err));
    goto bail;
  }
  setup_mdns(); // allow a failure
  return 0;

bail:
  esp_mqtt_client_destroy(MQTTHandle);
  return -1;
}

// HX711
int setup_sensors(void){
  Load.begin(HX711_DT, HX711_SCK);
  Load.set_scale(LoadcellScale);
  return 0;
}

void set_led(const struct failure_indication *nin){
  neopixelWrite(RGB_BUILTIN, nin->r, nin->g, nin->b);
}

void set_failure(const struct failure_indication *fin){
  if(fin != &PostFailure){
    StartupFailure = true;
  }
  set_led(fin);
}

void set_motor_pwm(void){
  set_pwm(MOTOR_CHAN, MotorPWM);
  // bring standby pin low if we're not sending any pwm, high otherwise
  if(MotorPWM == 0){
    digitalWrite(MOTOR_SBYPIN, LOW);
  }else{
    digitalWrite(MOTOR_SBYPIN, HIGH);
  }
}

// TB6612FNG
int setup_motor(gpio_num_t sbypin, gpio_num_t pwmpin, gpio_num_t pin1, gpio_num_t pin2){
  pinMode(sbypin, OUTPUT);
  pinMode(pin1, OUTPUT);
  pinMode(pin2, OUTPUT);
  pinMode(pwmpin, OUTPUT);
  initialize_pwm(MOTOR_CHAN, pwmpin, 490, LEDC_TIMER_3);
  set_motor_pwm();
  return 0;
}

void setup(void){
  neopixelWrite(RGB_BUILTIN, PreFailure.r, PreFailure.g, PreFailure.b);
  Serial.begin(115200);
  printf("dankdryer v" VERSION "\n");
  if(!init_pstore()){
    if(!read_pstore()){
      UsePersistentStore = true;
    }
  }
  if(setup_esp32temp()){
    set_failure(&SystemError);
  }
  if(setup_fans(LOWER_PWMPIN, UPPER_PWMPIN, LOWER_TACHPIN, UPPER_TACHPIN)){
    set_failure(&SystemError);
  }
  if(setup_motor(MOTOR_SBYPIN, MOTOR_PWMPIN, MOTOR_1PIN, MOTOR_2PIN)){
    set_failure(&SystemError);
  }
  if(setup_sensors()){
    set_failure(&SystemError);
  }
  if(setup_network()){
    set_failure(&NetworkError);
  }
  //gpio_dump_all_io_configuration(stdout, SOC_GPIO_VALID_GPIO_MASK);
  if(!StartupFailure){
    set_failure(&PostFailure);
  }
  printf("initialization %ssuccessful v" VERSION "\n", StartupFailure ? "un" : "");
}

// we don't try to measure the first iteration, as we don't yet have a
// timestamp (and the fans are spinning up, anyway).
int getFanTachs(unsigned *lrpm, unsigned *urpm){
  static uint32_t m;
  int ret = -1;
  if(m){
    const uint32_t diffu = micros() - m; // FIXME handle wrap
    *lrpm = LowerPulses;
    *urpm = UpperPulses;
    printf("raw: %u %u\n", *lrpm, *urpm);
    *lrpm /= 2; // two pulses for each rotation
    *urpm /= 2;
    const float scale = 60.0 * 1000000u / diffu;
    printf("scale: %f diffu: %lu\n", scale, diffu);
    *lrpm *= scale;
    *urpm *= scale;
    ret = 0;
  }else{
    *lrpm = UINT_MAX;
    *urpm = UINT_MAX;
  }
  m = micros();
  LowerPulses = 0;
  UpperPulses = 0;
  return ret;
}
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
void loop(void){
  float ambient = getAmbient();
  float weight = getWeight();
  printf("esp32 temp: %f weight: %f\n", ambient, weight);
  printf("pwm-l: %lu pwm-u: %lu\n", LowerPWM, UpperPWM);
  unsigned lrpm, urpm;
  if(!getFanTachs(&lrpm, &urpm)){
    printf("tach-l: %u tach-u: %u\n", lrpm, urpm);
  }
  auto curtime = esp_timer_get_time();
  send_mqtt(curtime, ambient, lrpm, urpm, weight);
  delay(15000);
}

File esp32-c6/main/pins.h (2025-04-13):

#ifndef DANKDRYER_PINS
#define DANKDRYER_PINS

#include <driver/gpio.h>

// esp32-c6 mini-1u-h4 pin assignments

// https://docs.espressif.com/projects/esp-idf/en/stable/esp32c6/api-reference/peripherals/gpio.html
// 0--6 are connected to ADC1
#define LOWER_TACHPIN GPIO_NUM_0   // lower chamber fan tach
#define LOWER_PWMPIN  GPIO_NUM_1   // lower chamber fan pwm
#define THERM_DATAPIN GPIO_NUM_4   // analog thermometer (ADC1)
#define HALL_DATAPIN  GPIO_NUM_5   // hall sensor
// 4 and 5 are strapping pins
#define UPPER_PWMPIN  GPIO_NUM_6   // upper chamber fan pwm
#define UPPER_TACHPIN GPIO_NUM_7   // upper chamber fan tach
// 8 and 9 are strapping pins
#define FRESET_PIN    GPIO_NUM_9   // factory reset when held for 5s
// 12--13 are used for JTAG (not strictly needed)
#define MOTOR_GATEPIN GPIO_NUM_12  // MOSFET gate for motor
#define SDA_PIN       GPIO_NUM_13  // I2C clock
#define SCL_PIN       GPIO_NUM_14  // I2C data
// 15 is a strapping pin
#define SSR_GPIN      GPIO_NUM_15  // heater solid state relay
/*
#define LCD_RST_PIN   GPIO_NUM_18
#define LCD_SCL_PIN   GPIO_NUM_19
#define LCD_SDA_PIN   GPIO_NUM_20
#define LCD_DC_PIN    GPIO_NUM_21
#define LCD_CS_PIN    GPIO_NUM_22
*/
// 24--30 are reserved for SPI flash

// set the logic level for the pin, which ought have output enabled.
int gpio_level(gpio_num_t pin, bool level);

// gpio_reset_pin() disables input and output, selects for GPIO, enables
// pullup, and disables pulldown.
static inline int
gpio_setup(gpio_num_t pin, gpio_mode_t mode, const char *mstr){
  gpio_reset_pin(pin);
  esp_err_t err;
  if((err = gpio_set_direction(pin, mode)) != ESP_OK){
    fprintf(stderr, "failure (%s) setting %d to %s\n", esp_err_to_name(err), pin, mstr);
    return -1;
  }
  return 0;
}

static inline int
gpio_set_inputoutput_opendrain(gpio_num_t pin){
  return gpio_setup(pin, GPIO_MODE_INPUT_OUTPUT_OD, "input+output(od)");
}

static inline int
gpio_set_inputoutput(gpio_num_t pin){
  return gpio_setup(pin, GPIO_MODE_INPUT_OUTPUT, "input+output");
}

static inline int
gpio_set_input(gpio_num_t pin){
  return gpio_setup(pin, GPIO_MODE_INPUT, "input");
}

static inline int
gpio_set_output(gpio_num_t pin){
  return gpio_setup(pin, GPIO_MODE_OUTPUT, "output");
}

#endif

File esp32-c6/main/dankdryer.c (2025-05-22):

// intended for use on an ESP32-S3-WROOM-1
#include "networking.h"
#include "dankdryer.h"
#include "version.h"
#include "nau7802.h"
#include "heater.h"
#include "efuse.h"
#include "reset.h"
#include "pins.h"
#include "fans.h"
#include "ota.h"
#include <nvs.h>
#include <time.h>
#include <math.h>
#include <ctype.h>
#include <cJSON.h>
#include <string.h>
#include <esp_log.h>
#include <stdatomic.h>
#include <led_strip.h>
#include <nvs_flash.h>
#include <esp_timer.h>
#include <esp_system.h>
#include <driver/ledc.h>
#include <driver/gpio.h>
#include <esp_app_desc.h>
#include <hal/ledc_types.h>
#include <esp_idf_version.h>
//#include <esp32c6/rom/rtc.h>
#include <esp_adc/adc_cali.h>
#include <driver/i2c_master.h>
#include <driver/gpio_filter.h>
#include <driver/temperature_sensor.h>

#define TAG "main"

#define UUIDLEN 16
#define MAX_DRYREQ_TMP 150
#define MIN_DRYREQ_TMP 50
// minimum of 15s between mqtt publications
#define MQTT_PUBLISH_QUANTUM_USEC 15000000ul
// give tachs a 5s period to smooth them out
#define TACH_SAMPLE_QUANTUM_USEC 5000000ul

#define BOOTCOUNT_RECNAME "bootcount"
#define TAREOFFSET_RECNAME "tare"
#define ESSID_RECNAME "essid"
#define PSK_RECNAME "psk"
#define SETUPSTATE_RECNAME "sstate"
#define MQTTBROKER_RECNAME "mqttbroker"
#define MQTTTOPIC_RECNAME "mqtttopic"
#define MQTTUSER_RECNAME "mqttuser"
#define MQTTPASS_RECNAME "mqttpass"
#define LOAD_CELL_MAX 500000 // 5kg capable, at 10mg

static bool MotorState;
static bool StartupFailure;
static float LastWeight = -1.0;
static float TareWeight = -1.0;
static time_t DryEndsAt; // dry stop time in seconds since epoch
static uint32_t Bootcount;  // preserved across factory reset
static float LastLowerTemp;
static uint32_t TargetTemp; // meaningful iff DryEndsAt != 0
static uint32_t LastSpoolRPM;
static i2c_master_dev_handle_t NAU7802;
static i2c_master_bus_handle_t I2CMaster;
static uint32_t LastLowerRPM, LastUpperRPM;

// variables manipulated by interrupts
static _Atomic(uint32_t) HallPulses;

// ESP-IDF objects
static bool NAUAvailable;
static temperature_sensor_handle_t temp;

static void
pulse_isr(void* pulsecount){
  _Atomic(uint32_t)* pc = pulsecount;
  ++*pc;
}

static inline bool
rpm_valid_p(unsigned rpm){
  return rpm < 3000;
}

static inline bool
weight_valid_p(float weight){
  return weight >= 0 && weight <= LOAD_CELL_MAX;
}

int setup_intr(gpio_num_t pin, _Atomic(uint32_t)* arg){
  if(gpio_set_input(pin)){
    return -1;
  }
  esp_err_t e;
  gpio_pin_glitch_filter_config_t fconf = {
    .clk_src = SOC_MOD_CLK_XTAL,
    .gpio_num = pin,
  };
  gpio_glitch_filter_handle_t gfilter;
  if((e = gpio_new_pin_glitch_filter(&fconf, &gfilter)) != ESP_OK){
    ESP_LOGE(TAG, "error (%s) creating glitch filter on %d", esp_err_to_name(e), pin);
    return -1;
  }
  if((e = gpio_glitch_filter_enable(gfilter)) != ESP_OK){
    ESP_LOGE(TAG, "error (%s) enabling glitch filter on %d", esp_err_to_name(e), pin);
    return -1;
  }
  if((e = gpio_pullup_dis(pin)) != ESP_OK){
    ESP_LOGE(TAG, "error (%s) disabling pullup on %d", esp_err_to_name(e), pin);
    return -1;
  }
  if((e = gpio_pulldown_en(pin)) != ESP_OK){
    ESP_LOGE(TAG, "error (%s) enabling pulldown on %d", esp_err_to_name(e), pin);
    return -1;
  }
  if((e = gpio_set_intr_type(pin, GPIO_INTR_NEGEDGE)) != ESP_OK){
    ESP_LOGE(TAG, "failure (%s) installing %d interrupt", esp_err_to_name(e), pin);
    return -1;
  }
  if((e = gpio_isr_handler_add(pin, pulse_isr, arg)) != ESP_OK){
    ESP_LOGE(TAG, "failure (%s) setting %d isr", esp_err_to_name(e), pin);
    return -1;
  }
  if((e = gpio_intr_enable(pin)) != ESP_OK){
    ESP_LOGE(TAG, "failure (%s) enabling %d interrupt", esp_err_to_name(e), pin);
    return -1;
  }
  return 0;
}

// precondition: isxdigit(c) is true
static inline char
get_hex(char c){
  if(isdigit(c)){
    return c - '0';
  }
  c = tolower(c);
  return c - 'a' + 10;
}

float get_tare(void){
  return TareWeight;
}

float get_lower_temp(void){
  return LastLowerTemp;
}

unsigned long long get_dry_ends_at(void){
  return DryEndsAt;
}

unsigned long get_target_temp(void){
  return TargetTemp;
}

float get_weight(void){
  return LastWeight;
}

uint32_t get_spool_rpm(void){
  return LastSpoolRPM;
}

unsigned get_lower_rpm(void){
  return LastLowerRPM;
}

unsigned get_upper_rpm(void){
  return LastUpperRPM;
}

// if record is not present, set *str to NULL and *len to 0, and return ESP_OK.
// if we encounter an error, same deal but with an error code. otherwise, *str
// is a heap-allocated copy of the record, and *len is its length.
static esp_err_t
nvs_get_opt_str(nvs_handle_t nh, const char* recname, char** str, size_t* len){
  *str = NULL;
  *len = 0;
#define MAX_NVS_STR 512
  size_t blen = MAX_NVS_STR + 1;
  char* buf = malloc(blen);
  if(!buf){
    return ESP_ERR_NO_MEM;
  }
  esp_err_t err = nvs_get_str(nh, recname, buf, &blen);
  if(err == ESP_ERR_NVS_NOT_FOUND){
    ESP_LOGI(TAG, "no record '%s' in nvs", recname);
    free(buf);
    return ESP_OK;
  }else if(err){
    ESP_LOGE(TAG, "error (%s) reading %s", esp_err_to_name(err), recname);
    free(buf);
    return err;
  }
  size_t rlen = strnlen(buf, MAX_NVS_STR);
  if(rlen >= MAX_NVS_STR){
    ESP_LOGE(TAG, "invalid record '%s'", recname);
    free(buf);
    return ESP_ERR_INVALID_SIZE;
  }
  // FIXME maybe also check for sanity? all isprint() etc?
  *str = strdup(buf); // get a smaller allocation, maybe
  free(buf);
  if(!*str){
    return ESP_ERR_NO_MEM;
  }
  *len = rlen;
  ESP_LOGI(TAG, "read '%s' from nvs:%s", *str, recname);
  return ESP_OK;
#undef MAX_NVS_STR
}

// load broker, user, and password from flash if they are present. anything
// that is not present is initialized to an empty string. all strings are
// heap-allocated.
int read_mqtt_config(mqttconfig* config){
  config->broker = config->user = config->pass = config->topic = NULL;
  nvs_handle_t nvsh;
  esp_err_t err = nvs_open(NVS_HANDLE_NAME, NVS_READONLY, &nvsh);
  if(err){
    ESP_LOGE(TAG, "failure (%d) opening nvs:" NVS_HANDLE_NAME "", err);
    return -1;
  }
  size_t blen;
  if(nvs_get_opt_str(nvsh, MQTTBROKER_RECNAME, &config->broker, &blen) != ESP_OK){
    goto err;
  }
  if(nvs_get_opt_str(nvsh, MQTTUSER_RECNAME, &config->user, &blen) != ESP_OK){
    goto err;
  }
  if(nvs_get_opt_str(nvsh, MQTTPASS_RECNAME, &config->pass, &blen) != ESP_OK){
    goto err;
  }
  if(nvs_get_opt_str(nvsh, MQTTTOPIC_RECNAME, &config->topic, &blen) != ESP_OK){
    goto err;
  }
  nvs_close(nvsh);
  return 0;
#undef MAX_MQTT_RECORDLEN

err:
  nvs_close(nvsh);
  mqttconfig_free(config);
  config->broker = config->user = config->pass = config->topic = NULL;
  return -1;
}
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

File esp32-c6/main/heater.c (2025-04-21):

#include "dankdryer.h"
#include "heater.h"
#include "pins.h"
#include <esp_log.h>
#include <soc/adc_channel.h>
#include <esp_adc/adc_oneshot.h>
#include <driver/temperature_sensor.h>

#define TAG "therm"

static bool HeaterState;
static float LastUpperTemp;
static bool ADC1Calibrated;
static adc_channel_t Thermchan;
static adc_oneshot_unit_handle_t ADC1;
static adc_cali_handle_t ADC1Calibration;

// initialize and calibrate an ADC unit (ESP32-S3 has two, but ADC2 is
// used by wifi). ADC1 supports GPIO 0--6.
static int setup_adc_oneshot(adc_unit_t unit, adc_oneshot_unit_handle_t* handle,
                             adc_cali_handle_t* cali, bool* calibrated){
  *calibrated = false;
  adc_oneshot_unit_init_cfg_t acfg = {
    .unit_id = unit,
    .ulp_mode = ADC_ULP_MODE_DISABLE,
  };
  esp_err_t e;
  if((e = adc_oneshot_new_unit(&acfg, handle)) != ESP_OK){
    ESP_LOGE(TAG, "error (%s) getting adc unit", esp_err_to_name(e));
    return -1;
  }
  // the ADC is designed around a 1100mV maximum input value. the LMT87 send
  // a value between 3277 mV (-50C) and 538 mV (150C). to handle such values,
  // we need attenuate the input signal. 12dB gives us up to 2450 mV, the
  // furthest we can go. to get the full range, we'd need a voltage divider
  // (something like 1000 + 470 ought work well). we don't really care about
  // such low values, so 12dB it is.
  adc_oneshot_chan_cfg_t cconf = {
    .bitwidth = ADC_BITWIDTH_DEFAULT,
    .atten = ADC_ATTEN_DB_12,
  };
  if((e = adc_oneshot_config_channel(*handle, Thermchan, &cconf)) != ESP_OK){
    ESP_LOGE(TAG, "error (%s) configuring adc channel", esp_err_to_name(e));
    adc_oneshot_del_unit(*handle);
    return -1;
  }
  adc_cali_curve_fitting_config_t caliconf = {
    .bitwidth = cconf.bitwidth,
    .atten = cconf.atten,
    .unit_id = unit,
    .chan = Thermchan,
  };
  if((e = adc_cali_create_scheme_curve_fitting(&caliconf, cali)) != ESP_OK){
    ESP_LOGE(TAG, "error (%s) creating adc calibration", esp_err_to_name(e));
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

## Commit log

2024-09-14 replace ds18b20 with esp32-s3 on-chip thermostat
    [dankdryer.ino]
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2024-09-15 scad: fix the hotbox floor
    [core.scad, croom.scad, dehydrator.scad]
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2024-09-16 strengthen motor mount
    [croom.scad, hotbox.scad]
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2024-09-16 hotbox: use pyramids for corner connects instead of lame extruded triangles
    [hotbox.scad]
2024-09-16 hotbox: fix ceramic heater mount geometry, return to 80mm fan
    [hotbox.scad]
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2024-09-18 core.scad: define fanhole object, use it in hotbox #2
    [core.scad, croom.scad, hotbox.scad]
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2024-09-18 enlarge lms mounts, strengthen motor front mount #5 #2
    [core.scad, croom.scad, worm.scad]
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2024-09-18 croom: expand ac adapter holes by 2mm #3
    [core.scad, croom.scad, hotbox.scad]
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2024-09-18 croom: expand the LMS horizontal by 1.65mm, down to 0.062 difference from measured diag #5
    [croom.scad, hotbox.scad]
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2024-09-18 croom: channel for ac wires running to heater #21
    [croom.scad]
2024-09-18 hotbox: build fan supports all the way through hole
    [hotbox.scad]
2024-09-18 croom: constant-thickness xy walls of 2mm #12 #13
    [core.scad, croom.scad]
2024-09-18 croom: move ac channel back to match new wall thickness
    [croom.scad]
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2024-09-19 build up the central shaft centered around the load cell, bearing, and gear #11
    [core.scad, croom.scad, lowercoupling.scad]
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2024-09-20 esp32: use rgb led for startup failure feedback, set up event loop #16
    [dankdryer.ino]
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2024-09-20 esp32: register for wifi events using default loop
    [core.scad, croom.scad, hotbox.scad]
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2024-09-20 build lower part of the air shield into croom #10
    [core.scad, croom.scad]
2024-09-20 lowercoupling: remove the section blocking access to the load cell mount #10
    [core.scad]
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2024-09-20 get working octagon -> circle morph yay! #8
    [hotbox.scad, tween_example6.scad, tween_loft.scad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]
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2024-09-20 fix extrusion of fan mounts
    [core.scad]
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2024-09-22 croom: bring it up to z = 0 #34
    [core.scad, croom.scad]
2024-09-22 fix motor placement viz-a-viz motorholder
    [core.scad, croom.scad, motormount.scad]
2024-09-22 croom: walls to 3 from 2, kill achole FIXME
    [croom.scad, motormount.scad]
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2024-09-22 top should be able to plug into hotbox #8
    [core.scad, tween.scad]
2024-09-22 hole and mount for thermocouple in hotbox #36
    [hotbox.scad]
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2024-09-22 replace gaussed.png with render.png
    [hotbox.scad]
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2024-09-23 hotbox: expand slot for 150C thermocouple by 2mm
    [hotbox.scad]
2024-09-23 print upper loadcell mount distinctly from lower coupling
    [lowercoupling.scad]
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2024-09-25 worm: bring worm gear bore back down to 5.5 for motor match
    [core.scad]
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2024-09-25 hotbox: shorten corner hookups a bit
    [hotbox.scad]
2024-09-25 hotbox: shorten hbcorner screw
    [hotbox.scad]
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2024-09-25 fill in some of the open interior of hotbox
    [hotbox.scad]
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2024-09-25 croom: depression to thread in hotbox fan cabling #41
    [croom.scad]
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2024-09-25 hotbox: use arcs as floor cuts to match cylinder #38
    [hotbox.scad]
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2024-09-27 lift lmsmounts, add acmounts on missing corners
    [croom.scad]
2024-09-27 square out lmsmounts. bring acadapter mounts back home
    [croom.scad]
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2024-09-30 promote ceramic screw holes to M4 from M3
    [hotbox.scad]
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2024-10-05 reset tach pulses after sampling
    [dankdryer.ino]
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2024-10-07 hotbox: move top cut up, expand rc522 holes
    [hotbox.scad]
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2024-10-13 collect and print error on mqtt subscribe failure
    [dankdryer.ino]
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2024-10-13 go ahead and render shaft() as part of coupling.stl
    [coupling.scad]
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2024-10-14 extend out gear shaft to bring up to wormgear height
    [core.scad]
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2024-10-15 croom: raise air shield, kill rightside wire channel
    [croom.scad]
2024-10-15 reject arduino API; use ESP-IDF (#46)
    * update README for esp-idf
    * add internal CMake
    * prep to use esp-idf 5.3
    * no NAN in esp-idf
    * no RGB_BRIGHTNESS in esp-idf
    * include math.h for isnan()
    * no Serial in esp-idf
    * update github workflow for esp-idf
    * factor out ESPIDFVER
    * toplevel CMakeLists.txt
    * switch idf.py target to esp32s3
    * resolve esp_timer functionality
    * enable -wwrite-strings and MQTT protocol 5
    * network_state_e is not a type
    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
    [core.scad, coupling.scad]
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2024-10-15 workflow: move dryer-network.h sample correctly
    [core.scad, coupling.scad]
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2024-10-16 use gpio_set_output() everywhere to get reset
    [dankdryer.c]
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2024-10-16 coupling: enlarge shaft for stability
    [core.scad]
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2024-10-16 place dropworm correctly
    [core.scad]
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2024-10-16 correct gears in stl.ong
2024-10-16 esp: probe i2c bus for HX711 and BME680
    [Bearing_Ball_6200_2RS.STL, coupling.scad]
2024-10-18 shorten platform by 20mm, shorten worm gear by 10mm
    [core.scad, coupling.scad]
2024-10-18 esp32: set up ADC1 for GPIO10 using 12dB attenuation
    [core.scad]
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2024-10-23 croom: thinner walls to reduce printtime / weight
    [core.scad, croom.scad]
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2024-10-25 croom: fix mount shield
    [croom.scad]
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2024-10-25 call nau7802_{reset/poweron}
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2024-10-27 don't try to read ADC if we didn't detect NAU7802
    [dankdryer.c]
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2024-10-28 core: fixed length for fan screws
    [core.scad]
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2024-10-28 hotbox: fix relayv3 hole spacing
    [hotbox.scad]
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2024-10-29 lower croom, lower motormount, kill middle of wirechannel
    [core.scad, croom.scad]
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2024-10-29 croom: remove perfmounts until we update for new perfboard
    [croom.scad]
2024-10-29 get fanmounts back into croom with horrible hackery
    [core.scad]
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2024-10-31 orient perfboard correctly in croom
    [croom.scad]
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2024-11-04 thicken the lowest cylinder of the main gear
    [core.scad]
2024-11-04 move relay to the coolbox, rotate lms mounts, move perfboard towards wall
    [croom.scad, hotbox.scad]
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2024-11-04 strengthen the air shield
    [croom.scad]
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2024-11-06 don't report device as discovered if initialization fails
    [dankdryer.c]
2024-11-06 correct test sense on i2c initializations
    [dankdryer.c]
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2024-11-09 croom: fix bottom fan mounts
    [croom.scad]
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2024-11-10 fix sense of hx711_data_ready_p()
    [dankdryer.c]
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2024-11-12 no need for boardlifter; cables hold it in position
    [boardlifter.scad]
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2024-11-12 croom: use combined rocker switch + NEMA receptacle
    [croom.scad]
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2024-11-18 croom: break apart bottom and walls for better printing
    [croom.scad]
2024-11-18 croom: trim out the motormount a bit more
    [core.scad]
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2024-11-21 looks like httpd_register_uri_handler() works now, check for error
    [dankdryer.c]
2024-11-21 factory reset: disable motor and heater #24
    [dankdryer.c]
2024-11-24 reunite croom, remove lms mounts (absorbed onto PCB)
    [croom.scad]
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2024-11-25 scad: kill unused code, make bottom flush to ease printing
    [core.scad, croom.scad]
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2024-11-25 scad: revert worm gear changes
    [core.scad]
2024-11-25 scad: tighten the worm back up on the rotor #58
    [core.scad]
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2024-11-27 fix up setup_temp() for ADC1
    [dankdryer.c]
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2024-11-30 scad: design the top cupola that sheathes the motor #64
    [core.scad, coupling.scad]
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2024-12-02 scad: redesign lower coupling for vertical motor #63
    [core.scad, coupling.scad]
2024-12-02 scad: tighten up lower coupling, indicate polarity #63
    [core.scad, coupling.scad]
2024-12-02 scad: bevel lower coupling so it sits above bolt tops #63
    [core.scad, coupling.scad]
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2024-12-02 scad: hole in lower coupling for load cell bump
    [complete.scad, core.scad, coupling.scad]
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2024-12-03 scad: bevel outer rim of rotor sheath #66
    [core.scad]
2024-12-06 tighten up the cupola to avoid shifts #66
    [core.scad]
2024-12-06 tighten the cupola further closes #66
    [core.scad]
2024-12-06 sync pin map to schematic, add hall sensor at 37 #68
    [hotbox.scad]
2024-12-06 scad: add noctua to complete model, prep spool for animation
    [complete.scad, core.scad, croom.scad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]
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2024-12-07 Makefile: don't build croom; it's included in complete
    [iec.stl]
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2024-12-10 scad: replace ch with cupolarimh
    [core.scad]
2024-12-12 nimble trash code largely taken from tutorial, yuck
    [core.scad]
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2024-12-12 scad: draw innermost filament torus on all lines
    [core.scad]
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2024-12-14 replace 150C thermal limiter with 175C
    [core.scad]
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2024-12-14 croom: center PCB, add mounting hole for antenna #71
    [croom.scad]
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2024-12-20 fix resistor input to triac
    [dankdryer.kicad_pcb, offcard.kicad_sch]
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2024-12-26 take 3.3V to microboard rather than dividing 5V on return from hall sensor
    [LM35.kicad_sch, dankdryer.kicad_pcb, dankdryer.kicad_sch]
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2024-12-26 blockdiagram: replace relay with mosfet
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2025-01-04 tighten up pcb a bit more
    [LM35.kicad_sch, dankdryer.kicad_pcb, dankdryer.kicad_sch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]
2025-01-05 replace NAU7802SGI with NAU7802KGI i accidentally bought
    [LM35.kicad_sch, dankdryer.kicad_pcb, dankdryer.kicad_sch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]
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2025-01-21 esp32: decode reset reason on boot
    [dankdryer.c]
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2025-02-01 productionize microboard
    move 5v converter to microboard (#88)
    replace 01x02 and 01x03 screw terminals with 1x5 JST
    add microboard to main PCB with cuts
    integrate microboard into schematics
    use smt hall sensor and throughhole thermometer
    [dankdryer.kicad_pcb, dankdryer.kicad_sch, microboard.kicad_sch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]
2025-02-05 [croom] cut bottom corners on shears to fight warping #89
    [core.scad, croom.scad, dankdryer.kicad_pcb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]
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2025-02-07 kill wirechannels, tighten croom bottom
    [core.scad, croom.scad]
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2025-02-12 [croom] tighten antenna hole
    [croom.scad]
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2025-02-14 [kicad] fix 3dmodel for JST-VH-B5P connectors
    [dankdryer.kicad_pcb]
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2025-02-16 tighten ScrewThreads
    [hotbox.scad, top.scad]
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2025-02-18 complete.scad: fix colors
    [complete.scad, core.scad, croom.scad]
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2025-02-21 invert logic for gpio9, erp
    [dankdryer.kicad_pcb, dankdryer.kicad_sch, microboard.kicad_sch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]
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2025-02-24 Revert "kill microboard"
    This reverts commit e7a6377caa4ae73bc4ee8e255010d285ca4e6727.
    [microboard.kicad_sch]
2025-02-24 Revert "kill offcard project"
    This reverts commit e1ec86b02246e5c3ca0ad2dad03ba15eb483766c.
    [offcard.kicad_sch]
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2025-02-25 [coupling] fix platform bug that led to many print failures
    [complete.scad, core.scad, croom.scad]
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2025-02-26 [top] fix bug that led to overprinting top surface
    [top.scad]
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2025-02-28 [hotbox] replace heater mounting holes with mounting rods #92
    [hotbox.scad]
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2025-02-28 use core height of 81 instead of 80, to divide evenly by 0.3
    [core.scad]
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2025-03-04 warning about spool melting
    [core.scad, croom.scad]
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2025-03-04 [pcb] tighten it up, keep things away from miniboard
    [dankdryer.kicad_pcb, offcard.kicad_sch]
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2025-03-10 [scad] move mount() to common, use it for heater mounts in hotbox
    [core.scad, croom.scad, hotbox.scad]
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2025-03-12 [makefile] fix stl build
    [core.scad]
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2025-03-14 [kicad] tighten things up
    [dankdryer.kicad_pcb, microboard.kicad_sch, offcard.kicad_sch]
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2025-03-16 add hooks for factory reset handling #69
    [dankdryer.c, pins.h, reset.c]
2025-03-16 [croom] tighten RP-SMA hole
    [croom.scad, hotbox.scad]
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2025-03-18 [pcb] swap mosfet inputs
    [dankdryer.kicad_pcb, offcard.kicad_sch]
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2025-03-26 sync pin definitions to reality, fixes nau7802 detection yay
    [croom.scad]
2025-03-26 fix swapped upper fan pins
    [croom.scad, dankdryer.kicad_pcb]
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2025-04-07 implement factory reset interrupt handler closes #69
    [reset.c]
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2025-04-13 preserve bootcount across a factory reset
    [dankdryer.c]
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2025-04-19 use nau7802_read_scaled(), fixes load cell sampling i think
    [dankdryer.c]
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2025-04-21 redesign lower coupling for side of load cell #114
    [core.scad, coupling.scad]
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2025-05-22 allow mqtt broker to be specified over BLE. read optional MQTT config from NVS. kill off dryer-network.h, yay! #116
    [dankdryer.c, networking.c, networking.h]
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2025-05-22 add mqttconfig_free(), use it in read_mqttconfig() error path
    [dankdryer.c, networking.c, networking.h]
2025-05-22 [BLE] don't allow MQTT broker without MQTT topic
    [networking.c]
2025-05-22 BLE reset callback log as error
    [networking.c]
